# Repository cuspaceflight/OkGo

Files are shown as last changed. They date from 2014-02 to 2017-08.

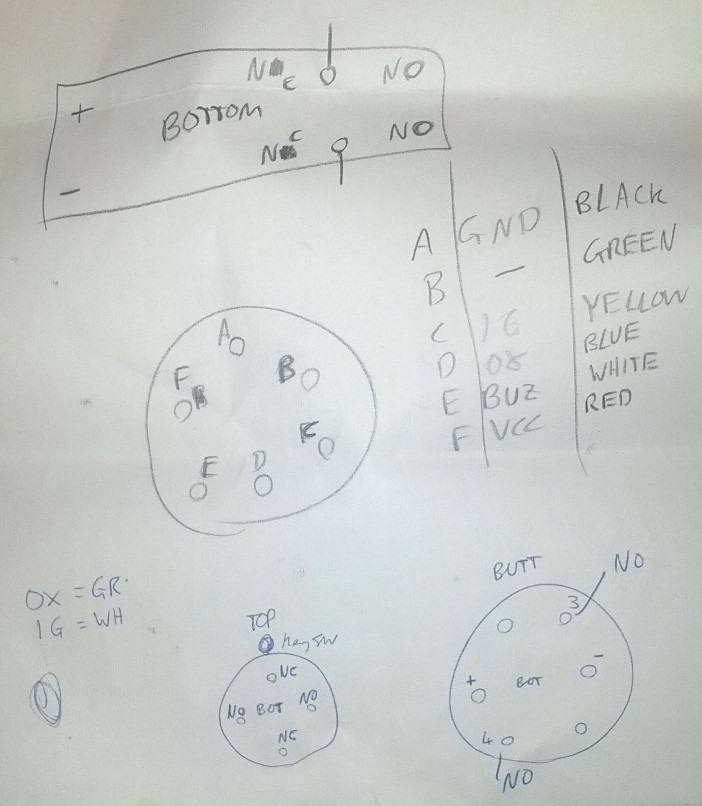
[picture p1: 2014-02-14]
OkGo/docs.jpg

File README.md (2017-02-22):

OkGo
====

*OkGo* is [Cambridge University Space Flight](http://cusf.co.uk)'s
rocket firing controller.

*OkGo* was designed for testing the *Quasar* hybrid rocket motor.  It allowed
remote (over 100m of wire) control of the nitrous oxide valve and firing of the
ignition e-match.  It was constructed using an ad-hoc point-to-point layout.
An entirely passive design, it simply uses mechanical switches to trigger
relays.  It was later upgraded to control two valves, one of which passed a low
flow of nitrous oxide to help start the motor.

*OkGo 2* was a full redesign for the launch of *Martlet 2*.  Due to the
increased safety radius (on the order of 500m) radio control is to be used.  It
will have 4 general purpose (valve or e-match) channels with independent
continuity checking and firing, and separate firing boxes containing current
limiting resistors.

*OkGo 3* is another full redesign for the launch of *Martlet 3*.  It will
continuity check and ignite a single channel with a constant-current drive.
Ignition and control will be small and light for portability.

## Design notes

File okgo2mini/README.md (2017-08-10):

# Design
* A mini version of OkGo 2 ignition, compatible with OkGo 2 control
* Use STM32F0 and RFM95W circuit from OkGo 2 ignition
    * If I'm careful I could make it pin-compatible and use the same firmware
      as OkGo 2, or just with minimal modification
* Use battery charge/management circuit from Toad/Linetime
    * Has only had minimal testing on Linetime. Wait for Toad to be tested
      before committing to this.
* Use 1A constant current firer from latest m3pyro
# Parts
* Nana plugs: red CN16308 black CN16305
* High retention red USB-B 1753809
* Red Hammond extruded aluminium case 2469292

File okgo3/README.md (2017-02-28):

# OkGo 3
## Features
* Single channel
* Continuity measurement
* Constant 4A current firing for e-matches
* Built-in battery (3.7V 2Ah)
* Charge from USB (400mA)
* Small and light
* Maybe easily detachable BNC antennas?
* Config and firmware upgrade over USB?

## Parts
* Case: Hammond 1553WCGY for control. Peli 1010 clear/yellow for ignition
* Battery: Cool Components 157 (Charge 400mA discharge 4A).
* Battery management bq24232HA
* Antenna: RF00075 ? Because it'll be easily detachable? But you really want it
  to be VPOL. And it's gross to put the BNC on the top.  Maybe same pivot
  swivel as on OkGo 2 Ignition?
* USB-B for charging because it's easy to clean the gunk out of.
* Ignition and control have touchscreen: ERC12864F7-4

## Thoughts
* Make both PCBs the same? They share the radio, battery, charging,
  on/off switch, case, USB, display and touchscreen
* Differences is ignition has banana jacks, control has fire button and
  keyswitch.
* Board-mount antenna connector on one end and cable-mount USB on other end
* Board mount nana jacks on front face or on one end?
* Control has display with touchscreen mounted to PCB which is mounted to top
  of the case, making display flush with top of case.  Antenna is an end-mount
  SMA which pokes out the end-panel.  Similarly for end-mount USB-B.
  Keyswitch, power switch and fire button???
* Ignition's touchscren is mounted to the board which sits in a sled in the
  bottom half of the peli - it's only accessible when you open the case.
  Charge USB is internal use only.  End-mount SMA goes to a pigtail to the
  external panel-mounted antenna SMA.
* Both have batteries mounted to the bottom of the PCB using a double-sided
  glue pad or possibly adhesive velcros.  Control's battery is in a void in the
  case, ignition's battery sits in a cut-out in the 3d printed sled.

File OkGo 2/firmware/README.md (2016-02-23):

OkGo2 Firmware
==============

# Getting started
## Grab the toolchain:
`sudo add-apt-repository ppa:terry.guo/gcc-arm-embedded`

`sudo apt-get update`

`sudo apt-get install gcc-arm-none-eabi`

**IF YOU FORGET TO ADD THE TERRY.GUO REPO YOU WILL GET MYSTERIOUS BUILD ERRORS
LIKE**

`arm-none-eabi-gcc: error: nano.specs: No such file or directory`

## Build libopencm3
* Run `git submodule update --init` to grab the libopencm3 repo
* Run `make` in `libopencm3/`
* **IF YOU FORGET THE PREVIOUS STEP YOU WILL GET MYSTERIOUS BUILD ERRORS LIKE**
  `No rule to make target 'main.elf'`.

## Setting a key
To authenticate both sides of the link, a symmetric pre-shared key is used.
This is stored in `common/key.h`.  An example file is provided at
`common/key_template.h`.  **The firmware will not build until a key
is set**.  To do this, copy `key_template.h` to `key.h`, change the key to
something random, and uncomment the relevant lines.

# Workflow
## Building firmware
* Run `make` in `control/` or `ignition/` as appropriate

## Programming
* `make flash` in `control/` or `ignition/` to program appropriate firmware
  using a BlackMagic programmer.

## Debugging
* More detailed info [_here_](http://darkdust.net/files/GDB%20Cheat%20Sheet.pdf)

### Getting started
* `make debug` to get an interactive debug session
* `arm-none-eabi-gdb foo.elf` or interactively `load foo.elf` and `file foo.elf`

### Printing info
* `p foo` / `print foo` to print `foo` in the current context
* `p/x foo` to print `foo` in hex

### Running
* `run` to run from beginning until break
* `start` to run until first line of `main()`
* `n` / `next` to step to next line
* `s` / `step` to step into a function
* `call myfunc()` to call a function

### Breaking
* `ctrl+c` to break wherever we happen to be
* `b function` / `b file.c:123` to add breakpoints on function call or line.
* `watch x` to break on change to variable `x`
* `d 1` to delete breakpoint 1
* `bt` / `where` for backtrace at current point

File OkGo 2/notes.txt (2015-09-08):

Firing cables
-------------
Banana jacks:
	Red: 1698956
	Yellow: 1698959
	Black: 1698957
Resistor:
	Need 2.5ohm with >60W handling
	RE03490 is 5ohm 50W for £1.5 - same as okgo1 I think.

Control 5V budget:
4x lightup button = 100mA
LCD = 150mA
total = 250mA

Control 3v3 budget:
30mA STM32
120mA RFM95W
337mA 5V budget scaled to 3v3
total = 487mA

Control battery wiring:
	Battery has JST-PH-F on short flying lead and sits on bottom half of case
	JST-PH-M Y-cable mounted on bottom half of case, to charge port on lower
	end-plate and to JST-PA on PCB.
	PCB routes battery via fuse to JST-PA for power button and then onwards.

STM32F071CBT Pin Assigning (control and ignition)
-------------
PC13,14,15 cannot source current and only sink 3mA and are limited to 2MHz into 30pF

USART locations:

10: USART4_TX
11: USART4_RX

12: USART2_TX
13: USART2_RX

21: USART3_TX
22: USART3_RX

ADC locations: pin 10-19 inc

SPI locations:

SPI1_NSS	14
SPI1_SCK 	15
SPI1_MISO	16
SPI1_MOSI	17

SPI1_NSS	38
SPI1_SCK	39
SPI1_MISO	40
SPI1_MOSI	41

SPI2_NSS	25
SPI2_SCK 	21
SPI2_MISO	27
SPI2_MOSI	28

SPI2_NSS	46
SPI2_SCK	26
SPI2_MISO	27
SPI2_MOSI	28

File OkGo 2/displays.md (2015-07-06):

#16x2:

    +----------------+
    |4.2V 6.4V  08/32|
    |ERR ERR ERR ERR |
    +----------------+
    +----------------+
    |4.2V 6.4V  08/32|
    |FIR OK  OK  ERR |
    +----------------+
    +----------------+
    |4.2V ?.?V  00/32|
    |    NO LINK     |
    +----------------+

#16x4:

    +----------------+
    |CBAT IBAT   RSSI|
    |4.2V 6.4V  08/32|
    |            CON |
    |FIR OK  OK  ERR |
    +----------------+
    +----------------+
    |CBAT IBAT   RSSI|
    |4.2V ?.?V  00/32|
    |    NO LINK     |
    |                |
    +----------------+

#20x2:

    +--------------------+
    |C4.2V I3.6V RSI08/32|
    |FIRE OK   OK   CERR |
    +--------------------+
    +--------------------+
    |C4.2V I?.?V RSI00/32|
    |      NO LINK       |
    +--------------------+

#20x4:

    +--------------------+
    |CBAT:4.2V  IBAT:6.4V|
    |    LINK: 08/32     |
    |CONT CONT CONT CONT |
    |ERR  ERR  ERR  ERR  |
    +--------------------+
    +--------------------+
    |CBAT:4.2V  IBAT:6.4V|
    |    LINK: 08/32     |
    |               CONT |
    |FIRE OK   OK   ERR  |
    +--------------------+
    +--------------------+
    |CBAT:4.2V  IBAT:?.?V|
    |    LINK: 00/32     |
    |      NO LINK       |
    |                    |
    +--------------------+

Possible metering display:

    +--------------------+
    |CBAT:4.2V  IBAT:6.4V|
    |    LINK: 08/32     |
    |FIRE OK   OK   ERR  |
    |9.4A 004R 125R 14kR |
    +--------------------+

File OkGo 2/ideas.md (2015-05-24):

#General Layout
 * Two boxes, *Control* (people end) and *Ignition* (rocket end)
 * 4 generic channels
 * AVR or Arduino pro-mini for control on each side.
 * Probably make each board with a custom PCB with everything onboard
 * Both boxes IP64/65 -- dust tight, protected against casual water ingress
 * Might be cute if the boxes can attach to a camera tripod -- apparent the
  thead on this is "1/4-20 UNC" for standard consumer tripods.

#Radio Link
 * Up to 500m apart on vaguely flat terrain with no particularly gnarly
  blockages inbetween
 * SMA-mount swivel rubber ducky antennas on each end.
 * LORA sounds like a good thing for the radio link -- spread spectrum
   goodness.
 * 868MHz would be nicer than 433MHz so we can stay away from FRS/ham radios
 * Might as well go with 20dBm = 100mW if we can.
 * [HopeRF RFM95W-868](http://www.hoperf.co.uk/shop/RFM95W-868S2-RFM95W_868S2.html)
   is 20dBm 868MHz LORA, sounds thoroughly excellent.  Not cheap though.

#Power Supply
 * Both boxes with integrated LiPOs
    * Probably 3-4S in ignition to approximate the 12V most things want
    * 1S in control (makes it easier because control doesn't need balance
      charging, and 1S will happily LDO down to 3v3).
 * Charged by external standard balance charger
 * Exposing balance charge connections via custom 4-contact connection
  (only need about an amp per contact).
 * Make special cable from custom connector to 3S balance + two banana
  jacks

#Control Box
 * Nice key-switch to power the box and arm.
 * Indication of link status / arm -- bi-colour red/green LED
 * Indication of continuity per-channel -- bi-colour red/green LED in/on or
  next to each firing button.

#Ignition Box
 * Current arming system with beeper and extra loud/quiet switch
 * No integrated current limiting for e-matches, all 4 channels are
  generic 12V some amps brought out to banana screwdowns.
 * For connecting to e-matches use a banana to croc clip lead with
  integrated current limit resistor.  Firey end has banana plugs with
  replacable croc clips for when they get gnarly.

#Micros
 * STM32F071CBT6 seems legit, costs about £2.50, LQFP-48.
 * [The Insider's Guide to the STM32](http://www.hitex.com/fileadmin/pdf/insiders-guides/stm32/isg-stm32-v18d-scr.pdf)
   seems like a helpful getting started document.
 * [Onecall](http://onecall.farnell.com/stmicroelectronics/stm32f071cbt6/mcu-32bit-cortex-m0-48mhz-lqfp/dp/2432093)
   and [datasheet](http://www.farnell.com/datasheets/1835716.pdf).
 * I should read [this](http://www.st.com/web/en/resource/technical/document/application_note/CD00221665.pdf) about STM32 oscillators
 * RFM95W seems to have listed pin directions backwards for MISO/MOSI in
   datasheet.

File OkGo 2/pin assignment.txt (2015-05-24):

pin name in backets means reset has different function
FT = 5V tolerant IO
FTf = 5V tol IO FM+ capable
TTa = 3v3 tolerant ADC
TC = 3v3

PC14/PC15 default to OSC32

PA0-3: TTa
PA8-12: FT

PB0-1: TTA
PB2: FT
PB10-12: FT
PB13-14: Ftf
PB15: FT

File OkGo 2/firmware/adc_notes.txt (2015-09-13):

adc notes

12-bit adc
internal channels: V_ref, temperature, VBAT (VDD)
Single shot or scan, latter performs automatic conversion on a group of analog inputs.
Can be DMAed
Result stored in left- or right-aligned 16-bit register (set ALIGN in ADC_CFGR1 to decide)
Choose resolution 12- 10- 8- 6-bit
1us conversion for 12-bit and faster for lower res.
Use RES[1:0] in ADC_CFGR1 to set resolution

When ADC is disabled (ADEN=0), calibrate by setting ADCAL=1, then leave the ADC alone until calibration finishes and ADCAL=0.

Only touch ADEN and ADCAL when ADC is disabled
Only touch ADSTART and ADDIS when ADC enabled and no pending disable request
Only touch other config bits (ADC_*) when ADEN=1 and ADSTART=0 (no ongoing conversion)
Only touch ADSTP if ADC enabled and no pending disable request.

Select scan channels using CHSEL (set bits for channels we want, CH0-18) and SCANDIR

Program sampling time to allow sampling capacitor to charge, based on impedance of source.  ADC_SMPR->SMP[2:0] sets sample time as a number of ADC clock cycles.  Sample time is common to all channels.
Analog switch has R=1k and sampling capacitor is 8pF.  Input impedances are on the order of 10k.  This gives a 99% rise-time of 400ns.  

Dedicated ADC clock is 14MHz making each ADC clock 71ns.  For our 99% rise we need 400/71=6 ADC clocks, so go with 13.5.

For continuous conversion, set CONT=1 in ADC_CFGR1 then ADSTART=1 and it will go and go and go.  Each conversion result is stored in ADC_DR and an interrupt optionally interrupts.
EXTEN = 0x0 for software-only triggering.

Normal strobe ADCing just dumps everything into the same ADC_DR register.  For easy readback you need to DMA it to a circular buffer.

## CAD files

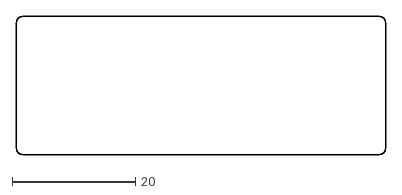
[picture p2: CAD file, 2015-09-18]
OkGo 2/cam/control_window_laser.dxf
60.0 x 22.5

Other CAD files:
OkGo 2/control/gerbers/control-F_Paste.dxf
OkGo 2/ignition/gerbers/ignition-F_Paste.dxf

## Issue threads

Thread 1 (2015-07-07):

De-specify SPI pins

cillian64, 2015-07-07:
On STM32F072 part, make the SPI pins not specified on the schematic part, as there are several choices for each.  I should also choose more carefully which pins I use based on PCB layout.

Closed 2015-07-07.

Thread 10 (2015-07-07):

Connect up nRST from SWDIO connector to STM32?

cillian64, 2015-07-07:

cillian64, 2015-07-08:
Yep, definitely.  This is (almost) correct (typo) on control, and apparently missing on ignition

Closed 2015-07-08.

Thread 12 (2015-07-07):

Relay failsafe circuit

cillian64, 2015-07-07:
Upstream relay on battery supply to firing relays.  Connect a sense line (with pulldown weaker than the 10k 3v3 sense pull-up) to the distribution between upstream and firing relays.  If any relays are welded this sense line will appear high while all relays are un-energised.

Closed 2015-07-08.

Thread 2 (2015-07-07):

Sort out mechanics

cillian64, 2015-07-07:
Think about cases for both sides, how to mount boards and switches and all the rest (panel mount, PCB mount?), how cases open and close, wire/board/panel connectors.

cillian64, 2015-08-14:
Control: start with display hole down. display bolts to standoffs on back of PCB, which bolts to standoffs on case's mounting lugs.  Arm, LED, keyswitch, firing buttons, all screw through front of case. Antenna goes through top plate, charge connector on bottom plate. Battery velcros to inside of case, probably on back half.

cillian64, 2015-08-14:
Ignition: Bottom of box is concave side.  PCB screws down to bottom brass-insert lugs covering entire bottom.  LiPO velcros and/or cable ties to PCB.  Antenna sticks out a side, everything else mounts through lid.

Closed 2015-08-14.

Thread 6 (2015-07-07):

Specify mechanical parts inc fixings

cillian64, 2015-07-07:

cillian64, 2015-08-20:
Ignition fixings:
4x 2x M? for neutriks
4x M3 for board to case

Control fixings:
2-4x M3 standoffs for board-case
2-4x M3 for board-standoffs
2-4x M? standoffs for LCD-board
2-4x M? screws for LCD-board

cillian64, 2015-08-27:
Screws Summary:
* 8x M3x20 pozi CS
* 4x M3x12 pozi pan/cheese
* 4x M3x6 pan
* 4x M3.5x12 pan

Nuts summary:
* 12x M3 full nuts
* lots x M3.5 full nuts

Washers summary:
* 24x M3 plain washers
* lots x M3.5 plain washers

cillian64, 2015-08-27:
Ordered

Closed 2015-08-27.

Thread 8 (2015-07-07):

Choose some connectors and stuff

cillian64, 2015-07-07:

cillian64, 2015-08-06:
Remaining:
Control
 - [ ] control charge
Ignition
 - [ ] ignition charge
 - [ ] ignition power-to-board
 - [ ] ignition firing
 - [ ] ignition firing-to-board

Closed 2015-08-14.

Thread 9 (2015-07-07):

Confirm footprints

cillian64, 2015-07-07:

cillian64, 2015-08-17:
Ignition:
 - SOD-123F [ ]
 - SOD-134FL [ ]
 - Switching reg [ ]
 - Relays [ ]
 - Fuse [ ]
 - JST-PA-2 upright [ ]

cillian64, 2015-08-17:
Control:
 - MSOP8 [ ]
 - JST-PA-2 RA [ ]
 - JST-PA-4 RA [ ]
 - Trimpot [ ]
 - LCD [ ]
 - Hammond 1553T [ ]
 - Polyfuse [ ]
 - Switching booster [ ]

cillian64, 2015-08-17:
Common:
 - R0805 [ ]
 - C0805 [ ]
 - C1206 [ ]
 - TVS 0603 [ ]
 - LQFP48 footprint [ ] pinout [ ]
 - RFM95W footprint [ ] pinout [ ]
 - SOT23 [ ]
 - Crystal [ ]
 - SMA-F [ ]
 - SWD [ ]
 - TP [ ]

Closed 2015-08-18.

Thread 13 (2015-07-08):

Add ESD diodes

adamgreig, 2015-07-08:
Should protect all the connectors with ESD diodes, especially power, antennas and firing channels. I like Farnell 2368169.

cillian64, 2015-07-08:
Similarly, remove the current pulldowns on the ignition outputs, they are entirely pointless.

cillian64, 2015-07-08:
I've been sneezing a lot lately so I'll get the 0603, [2368174](http://onecall.farnell.com/bourns/cga0603mlc-24e/esd-suppressor-0603-24v-0-5pf/dp/2368174).

Closed 2015-07-08.

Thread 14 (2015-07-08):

Test points

cillian64, 2015-07-08:

cillian64, 2015-07-08:
RFM and LCD are already easy enough to probe

Ignition: Vbatt, GND, 3v3, nRST, CONT_CH*, UPSTREAM_RELAY, RELAY_SENSE, FIRING_DIST, Firing channel outputs.

Control: Vbatt, GND, 3v3, nRST

Closed 2015-07-08.

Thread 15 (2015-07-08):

Check if drive resistor is on correct side of crystal / OSC_IN/OSC_OUT

cillian64, 2015-07-08:

Closed 2015-07-08.

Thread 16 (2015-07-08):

higher precision resistors for battery monitor

cillian64, 2015-07-08:
Accidentally used 5% resistors for the battery monitor divider, which is pretty poor...

cillian64, 2015-07-08:
Resolved.

Closed 2015-07-08.

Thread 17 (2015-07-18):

Change footprints to non-handsoldering

cillian64, 2015-07-18:
Will almost certainly mess up / have too much paste.

Closed 2015-07-18.

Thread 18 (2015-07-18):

Relay flyback diodes?

cillian64, 2015-07-18:

cillian64, 2015-07-18:
With flyback diode: ~1H coil (estimated from similar AC coil specs) gives 5mJ coil energy, dissipating in 0.015s in the coil resistance.

Closed 2015-07-18.

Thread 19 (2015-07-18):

USB interface

cillian64, 2015-07-18:
Bring GND,RX,TX,3v3 from STM32 UART to a JST-PA header on the board.

Connect this to some sort of 3-way or 4-way connector on the case.

Closed 2015-07-29.

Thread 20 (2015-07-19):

fix booster

cillian64, 2015-07-19:
5V "booster" is not actually a 5v booster.  Also check it's up to 250mA / 1.5W

boyuanxiao, 2015-07-21:
Is this about the Murata chip?  It looks alright: http://uk.mouser.com/ProductDetail/Murata-Power-Solutions/MEJ2S0305SC/?qs=pitIP5Ybo%2F%252bvVODbaEhTwg%3D%3D (sorry if you've already checked this...)

But if the ground is the same on either side it could be cheaper to go for a non-isolated converter?

cillian64, 2015-07-21:
Yep, this issue was before I updated the part  -- previously I'd accidentally put on a 3v3 - 3v3 converter (which was also not up to the current of all the LEDs and the LCD backlight!).  I forgot to close the issue when I fixed that.

A non-isolated converter would work fine but I didn't find one as convenient on my brief search of farnell.  I am open to suggestions.

cillian64, 2015-07-21:
(fixed in d90080b024b719421ce510433d57c2e19026046a)

boyuanxiao, 2015-07-21:
Cool - looks like most step up regulators which are cheaper will require getting the right inductors etc. Probably not worth the hassle if you're only getting one.

cillian64, 2015-07-21:
Yep, cost is quite low down on my priorities, so it's all about the convenience of something that Just Works (and it helps that it's a pretty small footprint compared to a DIY switch-mode booster)

Closed 2015-07-21.

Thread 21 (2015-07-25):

LCD voltages

cillian64, 2015-07-25:
Control's LCD is 5V.  Should be no problem to power VDD and V_LCD and V_LED from the 5V converter and it's V_IL is <3V so inputs are fine.  If we ever read back from it the respective STM32 pins will need to be 5V tolerant or otherwise clamped.  Do we ever need/want to read back from the display?

cillian64, 2015-07-29:
Clamped to read-only -- no problem.

Closed 2015-07-29.

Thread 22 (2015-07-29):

Make mechanical holes have correct clearance markers and unmask

cillian64, 2015-07-29:

cillian64, 2015-08-14:
Done as far as possible on control, not yet on ignition.

Closed 2015-08-15.

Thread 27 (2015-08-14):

Think about antenna connections and waterproofing

cillian64, 2015-08-14:

cillian64, 2015-08-17:
Waterproofing should be okay with an SMA gasket and hope the antenna copes -- easy enough to swap out if not and might be able to caulk up the joint.

Will worry more about SMA-F length when I have the ignition case and SMA-F and ANT.

cillian64, 2015-08-18:
Ignition will use vertical SMA with a pigtail (to be found).  Control happily fits with the end-plate.  Simple SMA gasket on both and hope for the best with the antenna.

Closed 2015-08-18.

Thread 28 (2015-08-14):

Routing of decoupling capacitors

cillian64, 2015-08-14:
Route power/ground to decoupling caps, not directly to pins.

Route to largest cap then down to smallest then to IC pins.  Where possible.

Closed 2015-08-14.

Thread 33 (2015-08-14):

Prep and order parts

cillian64, 2015-08-14:
Big farnell BOM
Arrange SWDs (from adam?)
RFM95Ws from hoperf.co.uk
Ignition case from Rapid/RS

cillian64, 2015-08-20:
Basically done.

Closed 2015-08-20.

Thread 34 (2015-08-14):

Design packet format

cillian64, 2015-08-14:
Fixed size/format packets, one from ignition->control, one control->ignition.

Basic inspiration: control sends packet ID, arm/disarm, fire ch1/ch2/ch3/ch4 every X interval
Ignition replies with same ID (as ack), cont ch1/ch2/ch3/ch4, batt voltage, relay sense, RSSI

cillian64, 2015-08-21:
First draft of protocols in 9c2f3c5

cillian64, 2015-09-15:
Seems like this has settled down.

Closed 2015-09-15.

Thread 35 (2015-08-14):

Lay out structure/flow of both firmwares

cillian64, 2015-08-14:

cillian64, 2015-08-21:
9c2f3c5 describes what's going on, now write skeletons

cillian64, 2015-09-18:
Give ignition a non-blocking receive and handle packet drops using a timer-check.  Nonblocking also means we can handle beepering

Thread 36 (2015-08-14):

Double-check DRC and ERC with correct design parameters

cillian64, 2015-08-14:

cillian64, 2015-08-18:
Relevant things:
 - Track width: .2mm / 8mil
 - Track gap/clearance: .2mm / 8mil
 - Min annular ring: .3mm / 12mil (CHECK VIAS)
 - Min hole: .4mm / 16mil (after plating)
 - Resist clearance: .08mm / 3mil
 - Min silk width: .15mm / 6mil

Closed 2015-08-19.

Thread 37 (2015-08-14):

I made a note that RFM95Ws have incorrect pin directions in datasheets -- double check this

cillian64, 2015-08-14:

cillian64, 2015-08-17:
Moved to confirm footprints, Issue #9

Closed 2015-08-17.

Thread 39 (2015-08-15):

put trimpot on ignition for buzzer

cillian64, 2015-08-15:
put mosfet series resistor before trimpot so turning volume down doesnt just ground stm32 output pin

cillian64, 2015-08-17:
Going to do this in software with the new control config menu.

Closed 2015-08-17.

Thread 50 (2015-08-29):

Correct LCD delays to appropriate us values

cillian64, 2015-08-29:
Actually enable crystal oscillator. Re"calibrate" delay functions and make a delay_us function and make LCD stuff use appropriate microsecond delays.

Closed 2015-09-13.

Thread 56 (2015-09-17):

Timers/timing based on sysclock instead of delays

cillian64, 2015-09-17:
For stuff like packet rate and the buzzer we want to have async delays based on sysclock, not delay_?s()

Closed 2015-09-19.

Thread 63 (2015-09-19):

Complain of booted armed

cillian64, 2015-09-19:
Control should refuse to turn on when armed,unless rebooting due to watchdog timer.

cillian64, 2015-09-19:
Resolved in 98670fe

Closed 2015-09-19.

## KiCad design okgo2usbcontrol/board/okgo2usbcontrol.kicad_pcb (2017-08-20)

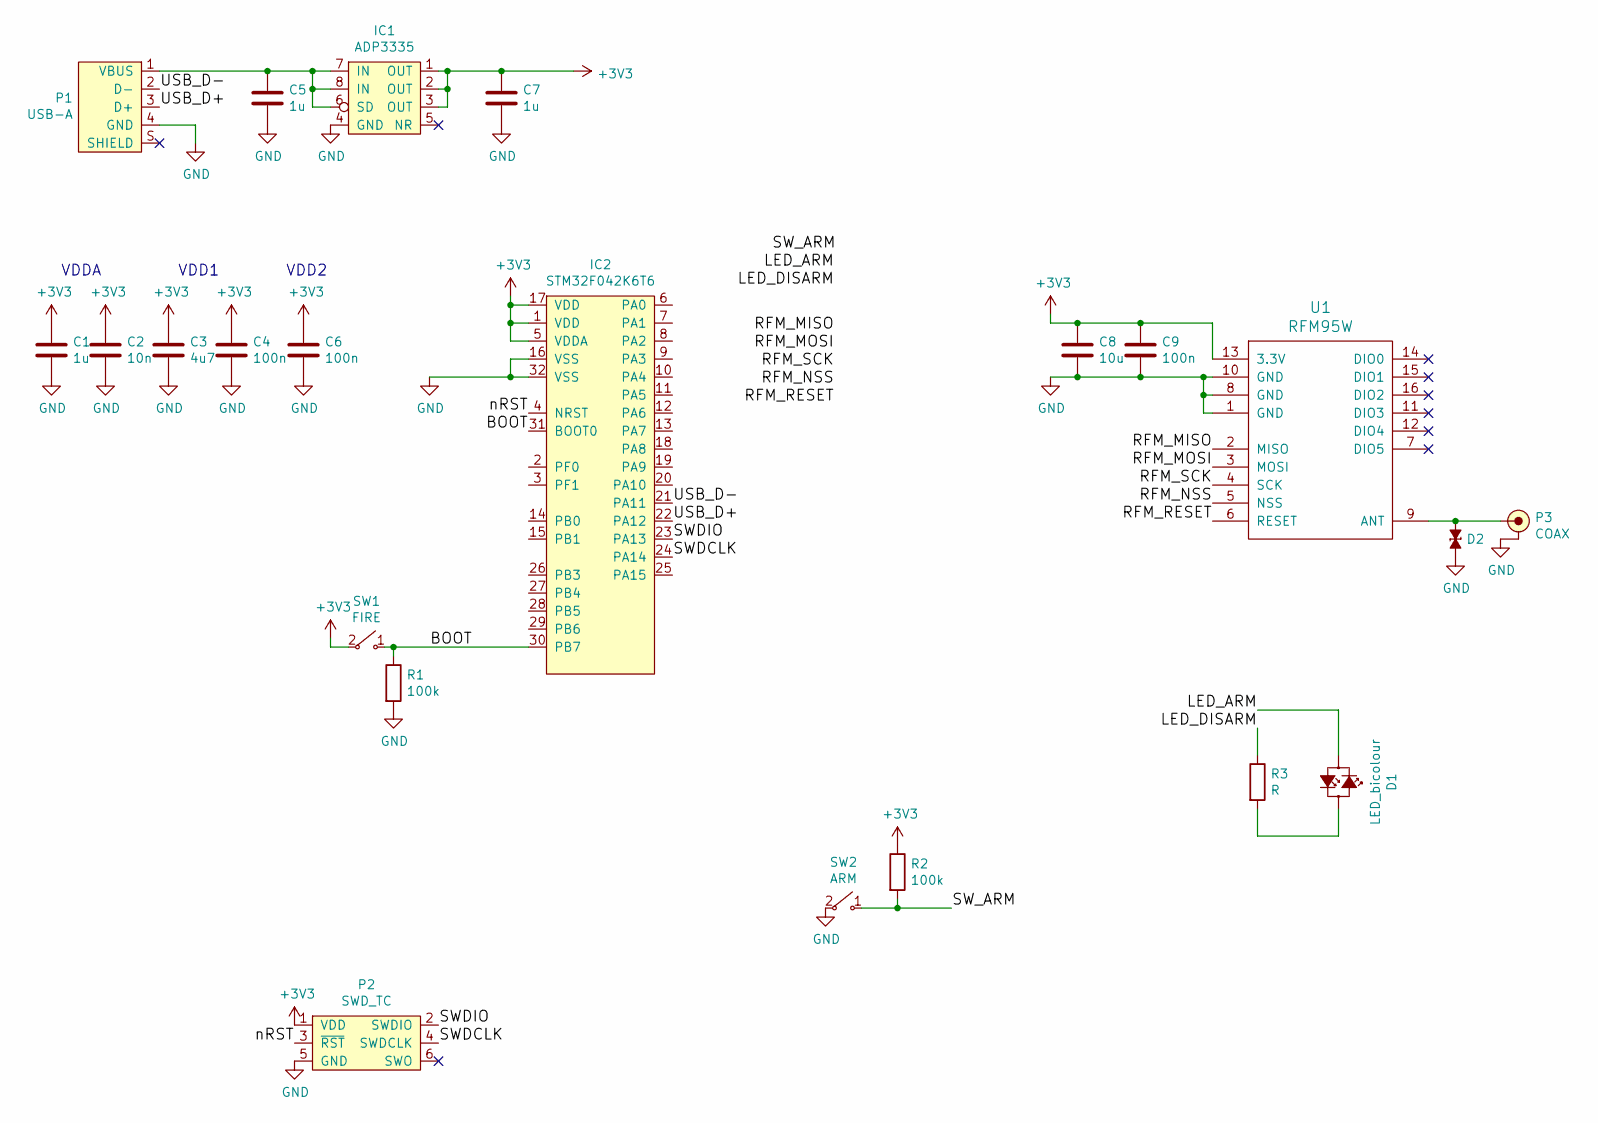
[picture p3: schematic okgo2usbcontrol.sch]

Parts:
C1, C5, C7: 1u; 0603
C2: 10n; 0603
C3: 4u7; 0603
C4, C6, C9: 100n; 0603
C8: 10u; 0603
D1: LED_bicolour; 0805-LED
D2: ESD_DIODE; 0603
IC1: ADP3335; MSOP-8; Farnell 2067775
IC2: STM32F042K6T6; LQFP-32; Farnell 2750629
P1: USB-A; USB-A_M_Edge; Farnell 2067044
P2: SWD_TC; TC2030-NL
P3: COAX; SMA-EDGE; Farnell 1608592
R1, R2: 100k; 0603
R3: R; 0603
SW1: FIRE; FSM2JSMx; Farnell 2610947
SW2: ARM; JSX08001SAQNL; Farnell 2435152
U1: RFM95W

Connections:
+3V3: C1.1, C2.1, C3.1, C4.1, C6.1, C7.1, C8.1, C9.1, IC1.1 (OUT), IC1.2 (OUT), IC1.3 (OUT), IC2.1 (VDD), IC2.5 (VDDA), IC2.17 (VDD), P2.1 (VDD), R2.1, SW1.2, U1.13 (3.3V)
/BOOT: IC2.30 (PB7), IC2.31 (BOOT0), R1.1, SW1.1
/LED_ARM: D1.1 (K)
/LED_DISARM: R3.1
/RFM_MISO: U1.2 (MISO)
/RFM_MOSI: U1.3 (MOSI)
/RFM_NSS: U1.5 (NSS)
/RFM_RESET: U1.6 (RESET)
/RFM_SCK: U1.4 (SCK)
/SWDCLK: IC2.24 (PA14), P2.4 (SWDCLK)
/SWDIO: IC2.23 (PA13), P2.2 (SWDIO)
/SW_ARM: R2.2, SW2.1
/USB_D+: IC2.22 (PA12), P1.3 (D+)
/USB_D-: IC2.21 (PA11), P1.2 (D-)
/nRST: IC2.4 (NRST), P2.3 (~RST)
GND: C1.2, C2.2, C3.2, C4.2, C5.2, C6.2, C7.2, C8.2, C9.2, D2.2, IC1.4 (GND), IC2.16 (VSS), IC2.32 (VSS), P1.4 (GND), P2.5 (GND), P3.2 (GND), R1.2, SW2.2, U1.1 (GND), U1.8 (GND), U1.10 (GND)
unnamed: C5.1, IC1.6 (SD), IC1.7 (IN), IC1.8 (IN), P1.1 (VBUS)
unnamed: D1.2 (A), R3.2
unnamed: D2.1, P3.1 (RF), U1.9 (ANT)

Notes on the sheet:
VDDA
VDD1
VDD2

Board: 2 copper layers, 22 parts (3 on the bottom side), 12 nets, no tracks yet.

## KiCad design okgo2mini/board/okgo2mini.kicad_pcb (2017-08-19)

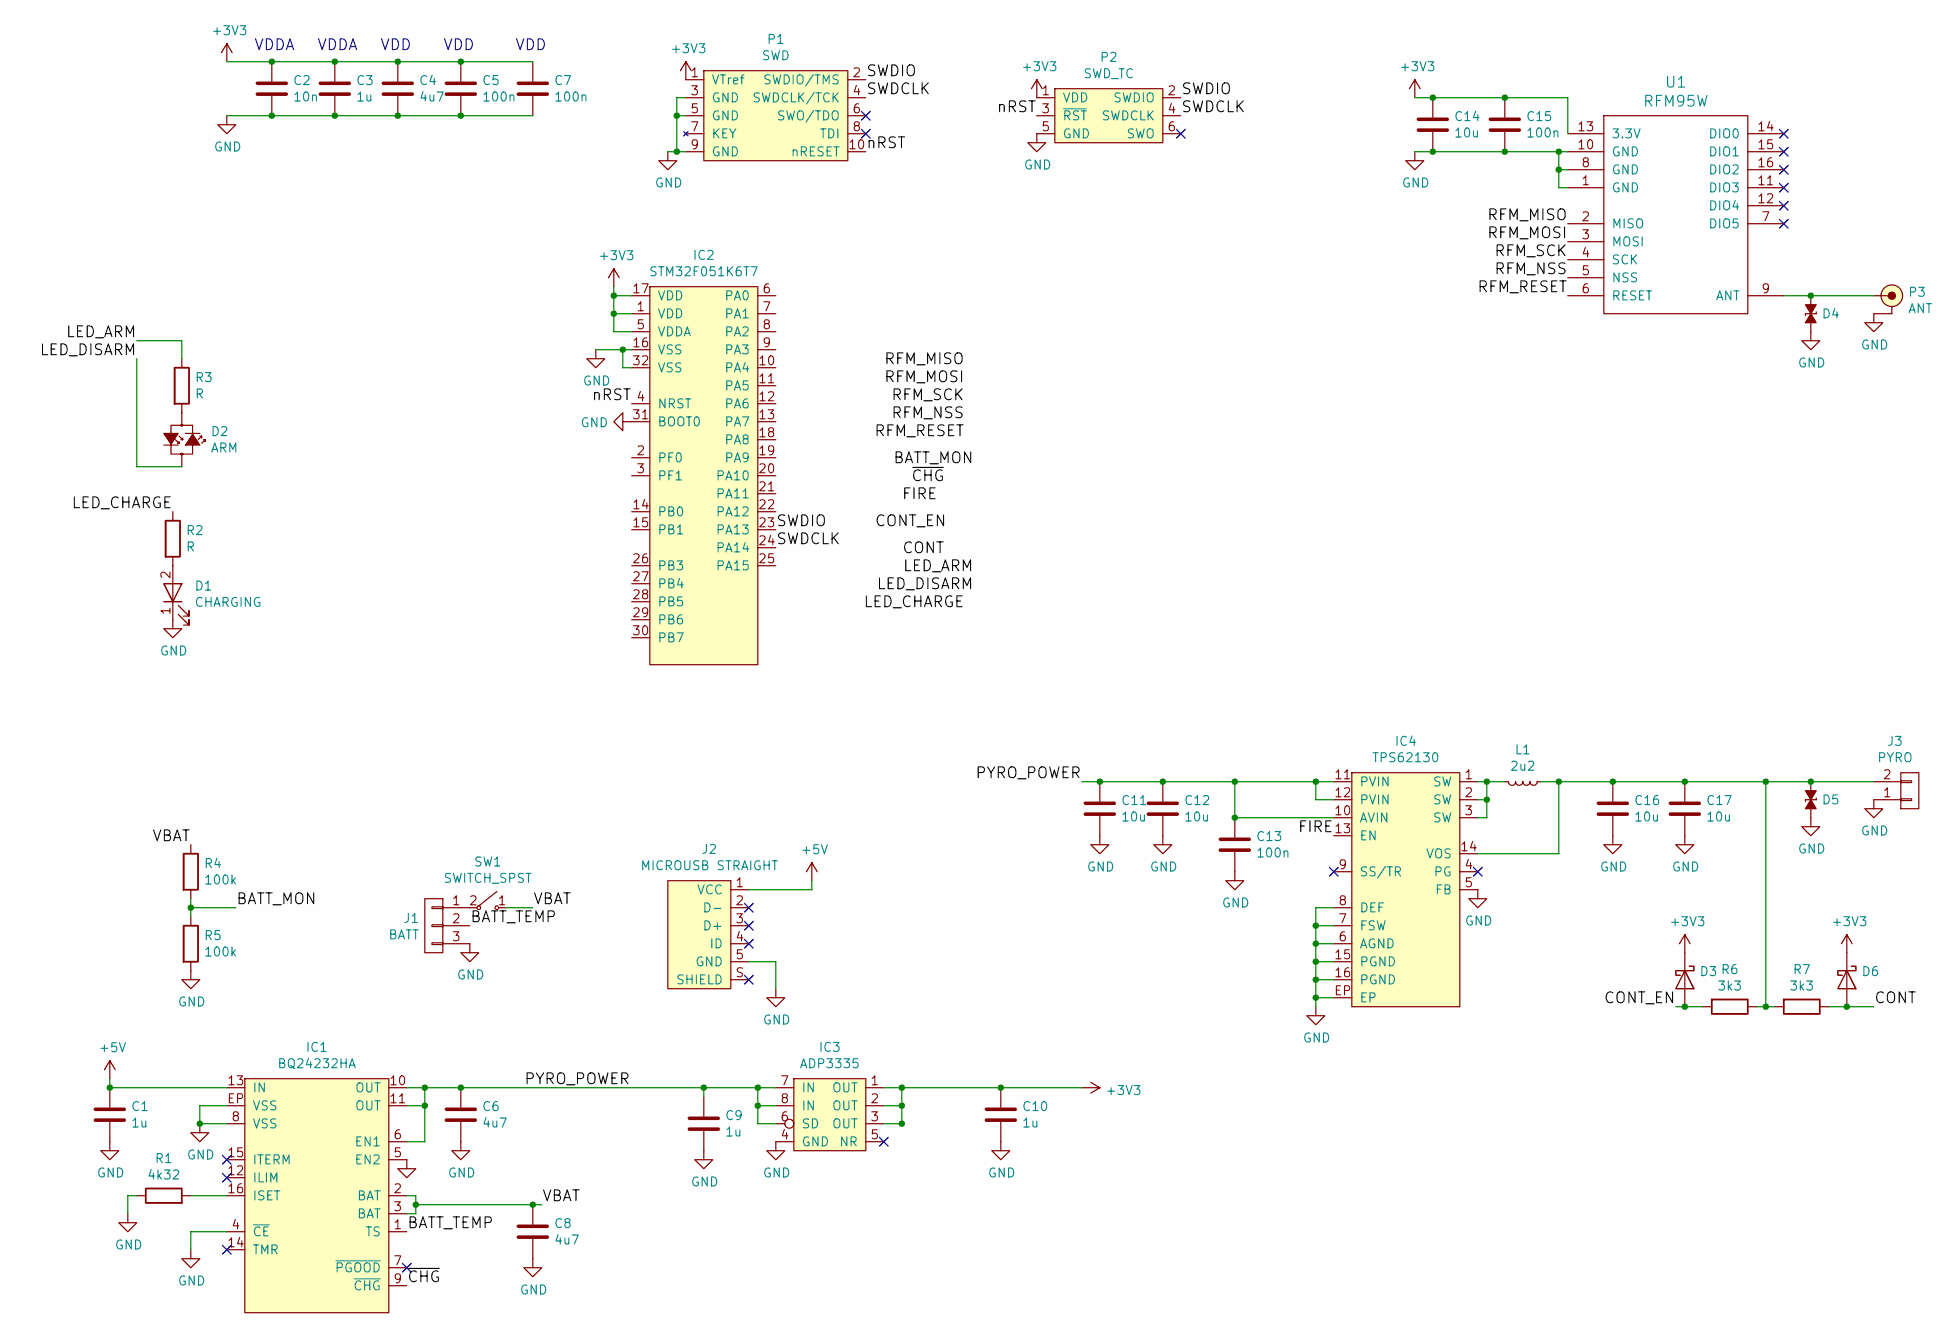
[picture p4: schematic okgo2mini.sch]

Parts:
C1, C3, C9, C10: 1u; 0603
C2: 10n; 0603
C4, C6, C8: 4u7; 0603
C5, C7, C13, C15: 100n; 0603
C11, C12, C14, C16, C17: 10u; 0603
D1: CHARGING; 0805-LED; Farnell 2610420
D2: ARM; 0805-LED; Farnell 2079908
D3, D6: PMEG2005AEA; SOD-323; Farnell 8737843
D4, D5: ESD_DIODE; 0603
IC1: BQ24232HA; QFN-16-EP-TI; Farnell 2576286
IC2: STM32F051K6T7; LQFP-32; Farnell 2432085
IC3: ADP3335; MSOP-8; Farnell 2067775
IC4: TPS62130; QFN-16-EP-TI; Farnell 2361246
J1: BATT; S03B-PASK-2
J2: MICROUSB STRAIGHT; USB_Micro_B_Vertical; Farnell 2614949
J3: PYRO; S02B-PASK-2
L1: 2u2; XFL4020; Farnell 2289216
P1: SWD; FTSH-105-01-F-D-K
P2: SWD_TC; TC2030-NL
P3: ANT; SMA-EDGE; Farnell 1608592
R1: 4k32; 0603
R2, R3: R; 0603
R4, R5: 100k; 0603
R6, R7: 3k3; 0603
SW1: SWITCH_SPST; 710xxxxV3xx; Farnell 9574743
U1: RFM95W

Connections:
+3V3: C2.1, C3.1, C4.1, C5.1, C7.1, C10.1, C14.1, C15.1, D3.1 (K), D6.1 (K), IC2.1 (VDD), IC2.5 (VDDA), IC2.17 (VDD), IC3.1 (OUT), IC3.2 (OUT), IC3.3 (OUT), P1.1 (VTref), P2.1 (VDD), U1.13 (3.3V)
+5V: C1.1, IC1.13 (IN), J2.1 (VCC)
/BATT_MON: R4.2, R5.1
/BATT_TEMP: IC1.1 (TS), J1.2
/CONT: D6.2 (A), R7.1
/CONT_EN: D3.2 (A), R6.2
/FIRE: IC4.13 (EN)
/LED_ARM: R3.1
/LED_CHARGE: R2.1
/LED_DISARM: D2.2 (A)
/PYRO_POWER: C6.1, C9.1, C11.1, C12.1, C13.1, IC1.6 (EN1), IC1.10 (OUT), IC1.11 (OUT), IC3.6 (SD), IC3.7 (IN), IC3.8 (IN), IC4.10 (AVIN), IC4.11 (PVIN), IC4.12 (PVIN)
/RFM_MISO: U1.2 (MISO)
/RFM_MOSI: U1.3 (MOSI)
/RFM_NSS: U1.5 (NSS)
/RFM_RESET: U1.6 (RESET)
/RFM_SCK: U1.4 (SCK)
/SWDCLK: IC2.24 (PA14), P1.4 (SWDCLK/TCK), P2.4 (SWDCLK)
/SWDIO: IC2.23 (PA13), P1.2 (SWDIO/TMS), P2.2 (SWDIO)
/VBAT: C8.1, IC1.2 (BAT), IC1.3 (BAT), R4.1, SW1.1
/nRST: IC2.4 (NRST), P1.10 (nRESET), P2.3 (~RST)
/~CHG: IC1.9 (~CHG)
GND: C1.2, C2.2, C3.2, C4.2, C5.2, C6.2, C7.2, C8.2, C9.2, C10.2, C11.2, C12.2, C13.2, C14.2, C15.2, C16.2, C17.2, D1.1 (K), D4.2, D5.2, IC1.4 (~CE), IC1.5 (EN2), IC1.8 (VSS), IC1.EP (VSS), IC2.16 (VSS), IC2.31 (BOOT0), IC2.32 (VSS), IC3.4 (GND), IC4.5 (FB), IC4.6 (AGND), IC4.7 (FSW), IC4.8 (DEF), IC4.15 (PGND), IC4.16 (PGND), IC4.EP, J1.3, J2.5 (GND), J3.1, P1.3 (GND), P1.5 (GND), P1.9 (GND), P2.5 (GND), P3.2 (GND), R1.1, R5.2, U1.1 (GND), U1.8 (GND), U1.10 (GND)
unnamed: C16.1, C17.1, D5.1, IC4.14 (VOS), J3.2, L1.1, R6.1, R7.2
unnamed: D1.2 (A), R2.2
unnamed: D2.1 (K), R3.2
unnamed: D4.1, P3.1 (RF), U1.9 (ANT)
unnamed: IC1.16 (ISET), R1.2
unnamed: IC4.1 (SW), IC4.2 (SW), IC4.3 (SW), L1.2
unnamed: J1.1, SW1.2

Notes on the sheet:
VDDA
VDD

Board: 2 copper layers, 43 parts (0 on the bottom side), 19 nets, no tracks yet.

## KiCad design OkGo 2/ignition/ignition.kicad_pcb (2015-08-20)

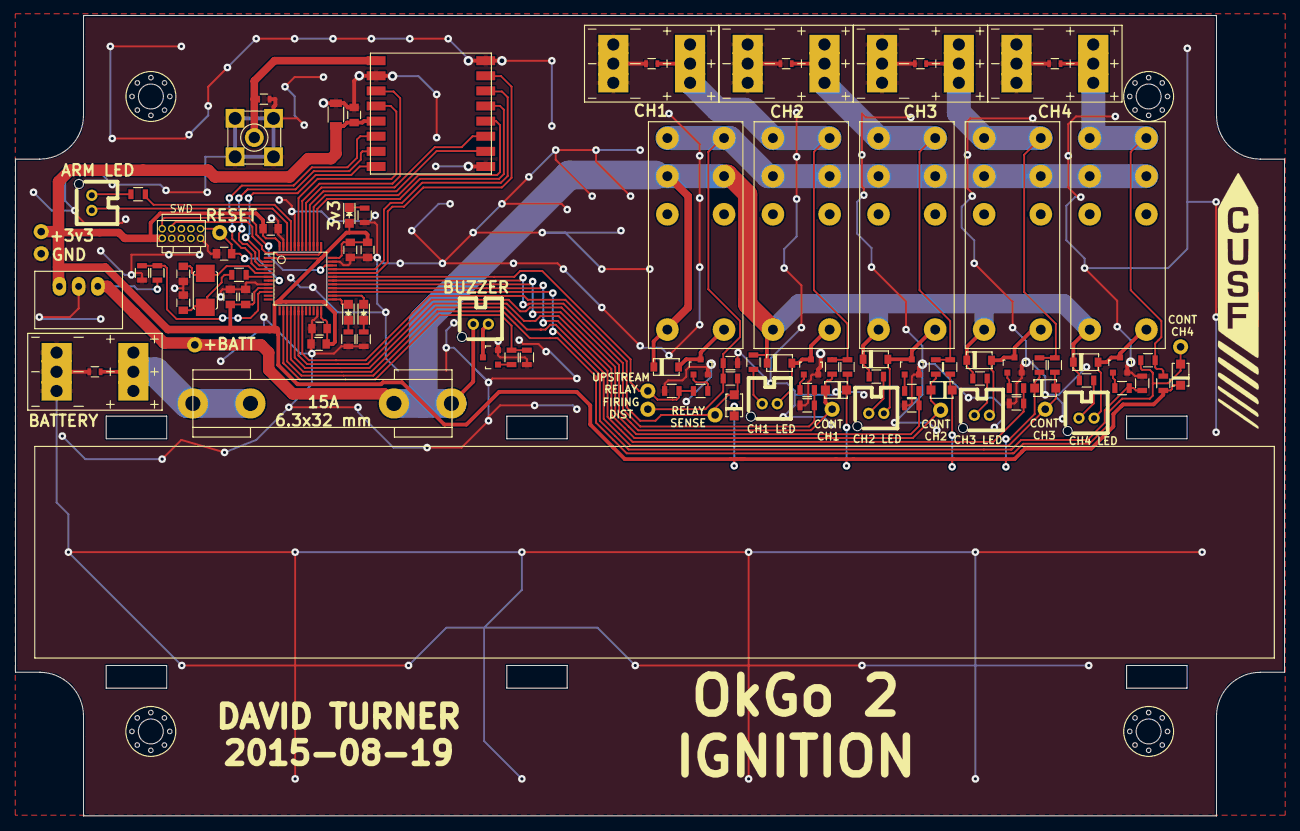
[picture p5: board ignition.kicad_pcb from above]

Board: 2 copper layers, 167.9 x 105.9 mm, 108 parts (0 on the bottom side), 63 nets.

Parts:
C101, C102, C104, C105, C109: 100n; C_0805
C103, C106: 4u7; C_0805
C107: 10n; C_0805
C108: 100u; C_1206
C110: 1u; C_0805
C111, C112: 15p; C_0805
D101, D103, D206, D210, D214, D218: TVS_small; R_0603
D104: RED; LED-0805
D105: GREEN; LED-0805
D106: YELLOW; LED-0805
D201, D205, D209, D213, D217: MBR2H200SFT1G; SOD-123FL
D202, D204, D208, D212, D216: D; SOD-123F
F101: 6.3x32; 6x32_fuseclip
K201, K202, K203, K204, K205: 16A SPST; Relay_RT314
M3_MOUNT, M3_MOUNT#2, M3_MOUNT#3, M3_MOUNT#4: VAL**; M3_MOUNT_FANCY
P105: BATT; PCB_SPADE
P107: ARM_LED; JST-PA-2-VERT
P109: BUZZ; JST-PA-2-VERT
P111: SMA; SMA_upright
P201: CH3_LED; JST-PA-2-VERT
P203: CH3; PCB_SPADE
P204: CH1_LED; JST-PA-2-VERT
P206: CH1; PCB_SPADE
P207: CH4_LED; JST-PA-2-VERT
P209: CH4; PCB_SPADE
P210: CH2_LED; JST-PA-2-VERT
P212: CH2; PCB_SPADE
Q101, Q201, Q202, Q203, Q204, Q205: BSS138BK; SOT-23
R101, R207, R212, R217, R222: 10k; R_0805
R102: 3k3; R_0805
R103: 75R; R_0805
R104: 100R; R_0805
R105, R201, R208, R213, R218, R223: 180R; R_0805
R106, R202, R204, R210, R214, R220, R224: 100k; R_0805
R107, R108, R109: R; R_0805
R203, R206, R211, R216, R221: 1k; R_0805
R205, R215: 430; R_0805
R209: 510R; R_0805
R219: 510; R_0805
TP101: BATT; TESTPOINT
TP102: GND; TESTPOINT
TP103: nRST; TESTPOINT
TP104: 3v3; TESTPOINT
TP201: FiringDist; TESTPOINT
TP202: USRelay; TESTPOINT
TP203: RelaySense; TESTPOINT
TP204: ContCH3; TESTPOINT
TP205: ContCH1; TESTPOINT
TP206: ContCH4; TESTPOINT
TP207: ContCH2; TESTPOINT
U103: SWD; FTSH-105-01-F-D-K
U105: RFM95W
U106: STM32F071CBT6; LQFP48_ST
U107: TSR 0.5-2433; TSR-0_5
Y101: 8MHz; XTAL50x32

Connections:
+3V3: C101.1, C102.1, C103.1, C105.1, C106.1, C107.1, C108.1, C109.1, C110.1, D104.2, D202.1, D204.1, D208.1, D212.1, D216.1, R206.1, R211.1, R216.1, R221.1, TP104.1, U103.1, U105.13, U106.1, U106.9, U106.24, U106.36, U106.48, U107.3
+BATT: D201.1, D205.1, D209.1, D213.1, D217.1, F101.2, K201.2, K201.3, K202.2, K203.2, K204.2, K205.2, P109.2, R101.1, R205.2, R209.2, R215.2, R219.2, TP101.1, U107.1
/ARM_LED: R103.2, U106.45
/BATT_MON: R101.2, R102.1, U106.10
/BUZZER: R105.2, R106.1, U106.14
/DISARM_LED: P107.1, U106.46
/RFM_DIO0: U105.14, U106.4
/RFM_DIO1: U105.15, U106.3
/RFM_DIO2: U105.16, U106.2
/RFM_DIO3: U105.11, U106.42
/RFM_DIO4: U105.12, U106.43
/RFM_DIO5: U105.7, U106.32
/RFM_MISO: U105.2, U106.40
/RFM_MOSI: U105.3, U106.41
/RFM_NSS: U105.5, U106.38
/RFM_RESET: U105.6, U106.33
/RFM_SCK: U105.4, U106.39
/SWDCLK: U103.4, U106.37
/SWDIO: U103.2, U106.34
/firing/CONT_CH1: D208.2, R212.1, TP205.1, U106.18
/firing/CONT_CH2: D216.2, R222.1, TP207.1, U106.17
/firing/CONT_CH3: D204.2, R207.1, TP204.1, U106.16
/firing/CONT_CH4: D212.2, R217.1, TP206.1, U106.15
/firing/FIRE_CH1: R213.2, R214.1, U106.30
/firing/FIRE_CH2: R223.2, R224.1, U106.29
/firing/FIRE_CH3: R208.2, R210.1, U106.28
/firing/FIRE_CH4: R218.2, R220.1, U106.27
/firing/FIRING_DIST: K201.4, K202.3, K203.3, K204.3, K205.3, R203.2, R204.1, TP201.1
/firing/RELAY_SENSE: D202.2, R203.1, TP203.1, U106.19
/firing/UPSTREAM_RELAY: R201.2, R202.2, TP202.1, U106.31
/nRST: C104.1, TP103.1, U103.10, U106.7
GND: C101.2, C102.2, C103.2, C104.2, C105.2, C106.2, C107.2, C108.2, C109.2, C110.2, C111.2, C112.2, D101.2, D103.2, D206.2, D210.2, D214.2, D218.2, P105.1, P111.2, P111.3, P111.4, P111.5, P203.1, P206.1, P209.1, P212.1, Q101.2, Q201.2, Q202.2, Q203.2, Q204.2, Q205.2, R102.2, R106.2, R107.2, R108.2, R109.2, R202.1, R204.2, R210.2, R214.2, R220.2, R224.2, TP102.1, U103.3, U103.5, U103.9, U105.1, U105.8, U105.10, U106.8, U106.23, U106.35, U106.44, U106.47, U107.2
unnamed: C111.1, R104.1, Y101.2
unnamed: C112.1, U106.5, Y101.1
unnamed: D101.1, F101.1, P105.2
unnamed: D103.1, P111.1, U105.9
unnamed: D104.1, R107.1
unnamed: D105.1, R108.1
unnamed: D105.2, U106.25
unnamed: D106.1, R109.1
unnamed: D106.2, U106.26
unnamed: D201.2, K201.1, Q201.3
unnamed: D205.2, K202.1, P201.1, Q202.3
unnamed: D206.1, K202.4, P203.2, R206.2, R207.2
unnamed: D209.2, K203.1, P204.1, Q203.3
unnamed: D210.1, K203.4, P206.2, R211.2, R212.2
unnamed: D213.2, K204.1, P207.1, Q204.3
unnamed: D214.1, K204.4, P209.2, R216.2, R217.2
unnamed: D217.2, K205.1, P210.1, Q205.3
unnamed: D218.1, K205.4, P212.2, R221.2, R222.2
unnamed: P107.2, R103.1
unnamed: P109.1, Q101.3
unnamed: P201.2, R205.1
unnamed: P204.2, R209.1
unnamed: P207.2, R215.1
unnamed: P210.2, R219.1
unnamed: Q101.1, R105.1
unnamed: Q201.1, R201.1
unnamed: Q202.1, R208.1
unnamed: Q203.1, R213.1
unnamed: Q204.1, R218.1
unnamed: Q205.1, R223.1
unnamed: R104.2, U106.6

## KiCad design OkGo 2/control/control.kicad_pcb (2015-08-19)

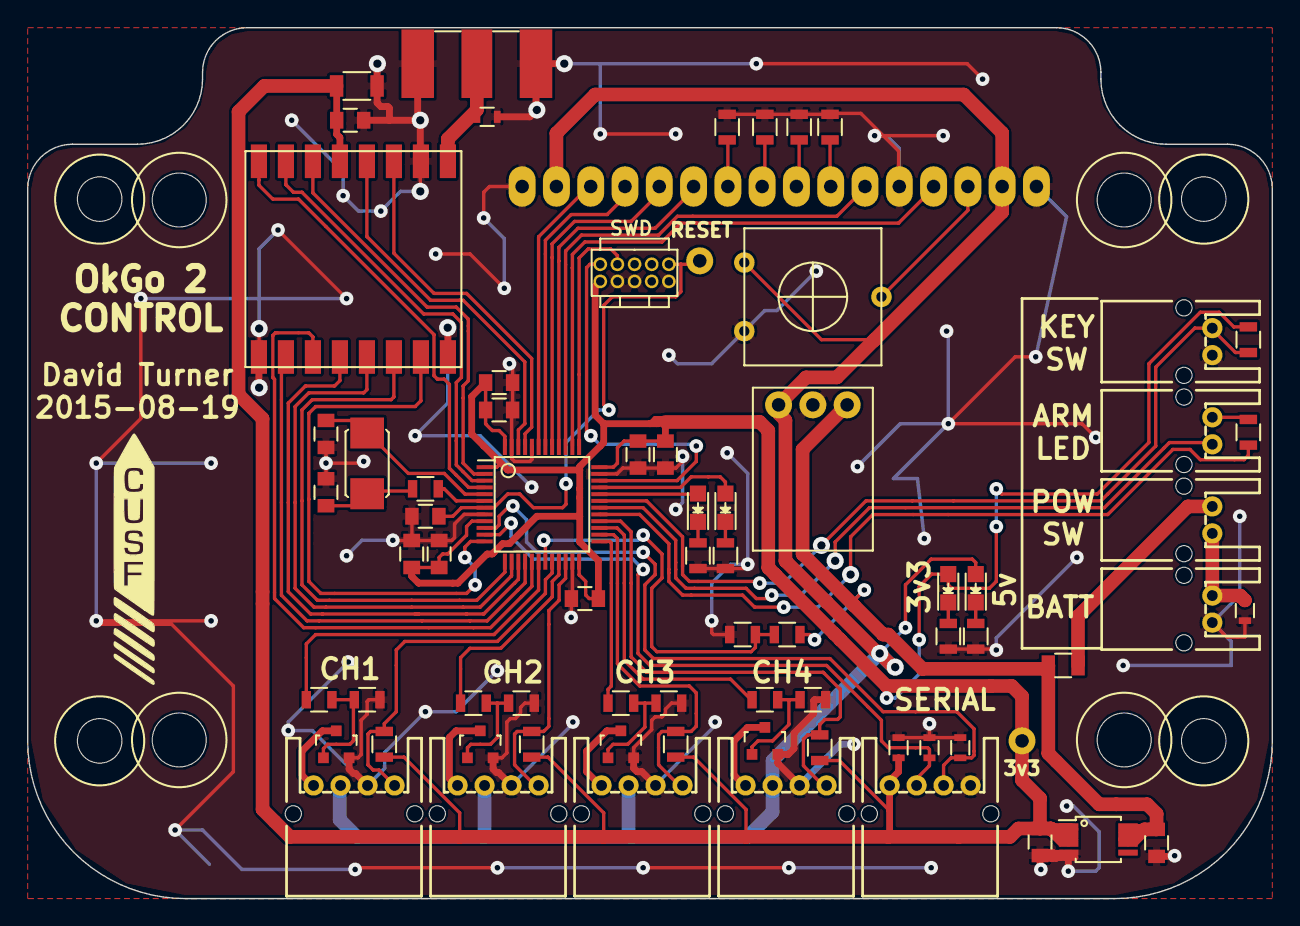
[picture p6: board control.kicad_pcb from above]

Board: 2 copper layers, 92.2 x 64.5 mm, 77 parts (1 on the bottom side), 64 nets.

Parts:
C101, C102, C104, C108, C112: 100n; C_0805
C103, C105: 4u7; C_0805
C106: 10n; C_0805
C107: 1u; C_0805
C109, C110: 15p; C_0805
C111: 100u; C_1206
C113, C114: 2u2; C_0805
D101, D103, D104, D105, D106: TVS_small; R_0603
D107, D110: RED; LED-0805
D108: GREEN; LED-0805
D109: YELLOW; LED-0805
F101: PTC; polyfuse0805
M3_MOUNT, M3_MOUNT#2, M3_MOUNT#3, M3_MOUNT#4: VAL**; M3_MOUNT
P102: KEYSW; JST-PA-2
P105: BATT; JST-PA-2
P106: ARM_LED; JST-PA-2
P108: SMA; SMA-142-0701-801
P110: POWER_SW; JST-PA-2
P111: SERIAL; JST-PA-4
P201: CH1; JST-PA-4
P202: CH2; JST-PA-4
P205: CH3; JST-PA-4
P206: CH4; JST-PA-4
Q201, Q202, Q203, Q204: BSS138BK; SOT-23
R101, R106, R107, R108, R109, R110, R205, R206, R211, R212: 10k; R_0805
R102: 100R; R_0805
R103: 75R; R_0805
R104: R_Small; R_0805
R105: 3k3; R_0805
R111, R112, R113: R; R_0805
R201, R202, R207, R208: 180R; R_0805
R203, R204, R209, R210: 100k; R_0805
RV101: 20k LIN; bourns3386G
TP101: nRST; TESTPOINT
TP102: 3v3; TESTPOINT
U101: SWD; FTSH-105-01-F-D-K
U102: STM32F071CBT6; LQFP48_ST
U103: pololu_S7V7F5; polulo_S7V7F5
U105: RFM95W
U106: LCD_HD44780; LCD_MC42004A6W_bare
U107: ADP3335; MSOP-8_3x3mm_Pitch0.65mm
Y101: 8MHz; XTAL50x32

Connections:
+3V3: C101.1, C102.1, C103.1, C104.1, C105.1, C106.1, C107.1, C111.2, C112.2, C114.1, D106.1, D107.2, P111.4, R101.1, R205.1, R206.1, R211.1, R212.1, TP102.1, U101.1, U102.1, U102.9, U102.24, U102.36, U102.48, U105.13, U107.1, U107.2, U107.3
+5V: D110.2, P201.3, P202.3, P205.3, P206.3, RV101.1, U103.3, U106.2, U106.15
+BATT: C113.1, F101.2, R105.1, U103.1, U107.6, U107.7, U107.8
/ARM_LED: R103.2, U102.29
/ARM_SW: P102.2, R101.2, U102.31
/BATT_MON: R105.2, R106.1, U102.19
/DISARM_LED: P106.1, U102.30
/LCD_DB4: U102.40, U106.11
/LCD_DB5: U102.41, U106.12
/LCD_DB6: U102.42, U106.13
/LCD_DB7: U102.43, U106.14
/LCD_E: U102.39, U106.6
/LCD_RS: U102.38, U106.4
/RFM_DIO0: U102.2, U105.14
/RFM_DIO1: U102.3, U105.15
/RFM_DIO2: U102.4, U105.16
/RFM_DIO3: U102.45, U105.11
/RFM_DIO4: U102.46, U105.12
/RFM_DIO5: U102.12, U105.7
/RFM_MISO: U102.16, U105.2
/RFM_MOSI: U102.17, U105.3
/RFM_NSS: U102.14, U105.5
/RFM_RESET: U102.13, U105.6
/RFM_SCK: U102.15, U105.4
/SWDCLK: U101.4, U102.37
/SWDIO: U101.2, U102.34
/controls/CH1_LED: R201.2, U102.18
/controls/CH1_SW: P201.1, R205.2, U102.20
/controls/CH2_LED: R202.2, U102.21
/controls/CH2_SW: P202.1, R206.2, U102.22
/controls/CH3_LED: R207.2, U102.25
/controls/CH3_SW: P205.1, R211.2, U102.26
/controls/CH4_LED: R208.2, U102.27
/controls/CH4_SW: P206.1, R212.2, U102.28
/nRST: C108.1, TP101.1, U101.10, U102.7
GND: C101.2, C102.2, C103.2, C104.2, C105.2, C106.2, C107.2, C108.2, C109.2, C110.2, C111.1, C112.1, C113.2, C114.2, D101.2, D103.1, D104.2, D105.2, D106.2, P102.1, P105.1, P108.2, P108.3, P108.4, P108.5, P111.1, P201.2, P202.2, P205.2, P206.2, Q201.2, Q202.2, Q203.2, Q204.2, R104.2, R106.2, R107.2, R108.2, R109.2, R110.2, R111.2, R112.2, R113.2, R203.2, R204.2, R209.2, R210.2, RV101.3, U101.3, U101.5, U101.9, U102.8, U102.23, U102.35, U102.44, U102.47, U103.2, U105.1, U105.8, U105.10, U106.1, U106.5, U106.16, U107.4
unnamed: C109.1, R102.2, Y101.2
unnamed: C110.1, U102.5, Y101.1
unnamed: D101.1, P105.2, P110.1
unnamed: D103.2, P108.1, U105.9
unnamed: D104.1, P111.2, U102.10
unnamed: D105.1, P111.3, U102.11
unnamed: D107.1, R104.1
unnamed: D108.1, R111.1
unnamed: D108.2, U102.33
unnamed: D109.1, R112.1
unnamed: D109.2, U102.32
unnamed: D110.1, R113.1
unnamed: F101.1, P110.2
unnamed: P106.2, R103.1
unnamed: P201.4, Q201.3
unnamed: P202.4, Q202.3
unnamed: P205.4, Q203.3
unnamed: P206.4, Q204.3
unnamed: Q201.1, R201.1, R203.1
unnamed: Q202.1, R202.1, R204.1
unnamed: Q203.1, R207.1, R209.1
unnamed: Q204.1, R208.1, R210.1
unnamed: R102.1, U102.6
unnamed: R107.1, U106.10
unnamed: R108.1, U106.9
unnamed: R109.1, U106.8
unnamed: R110.1, U106.7
unnamed: RV101.2, U106.3

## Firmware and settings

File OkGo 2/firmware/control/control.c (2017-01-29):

#include <stdint.h>
#include <stdbool.h>

#include <libopencm3/stm32/gpio.h>
#include <libopencm3/stm32/rcc.h>

/* Common includes */
#include "rfm95w.h"
#include "utils.h"

/* control-specific includes */
#include "control.h"
#include "control_radio.h"
#include "control_pins.h"
#include "display.h"
#include "adc.h"
#include "splash.h"

/* Configuration constants */
const uint16_t SLOW_PACKET_DELAY = 1000; /* delay in ms */
const uint16_t FAST_PACKET_DELAY = 250; /* delay in ms */
const uint32_t PACKET_DROP_DELAY = 2000;
const uint8_t RADIO_POWER_DBM = 10; /* Radio tx power in dBm */
const uint8_t MAX_RESISTANCE = 50; /* Max R in ohms of device otherwise CERR */

/* Internal functions */

/* Initialisation including clocks, pins, radio, state, ADCs */
void control_init(control_state *state, control_radio_state *radio_state);

/* Convert a channel status enum into a string and print to LCD */
void control_display_ch_status(uint8_t ch_status, bool remote_fire);

/* Display a continuity resistance to the LCD */
void control_display_ch_cont(uint8_t cont, uint8_t ch_status);

/* Update display from local state */
void control_display_update(control_state *state,
                            control_radio_state *radio_state);

void control_init(control_state *state, control_radio_state *radio_state)
{
    /* Initialise local state variables */
    state->armed = false;
    state->centre_frf = FRF_868;
    state->ch1_status = CH_STATUS_OK;
    state->ch2_status = CH_STATUS_OK;
    state->ch3_status = CH_STATUS_OK;
    state->ch4_status = CH_STATUS_OK;

    /* Setup crystal oscillator and systick */
    rcc_clock_setup_in_hsi_out_48mhz();
    systick_init();

    /* Clock GPIOs, set pin modes */
    control_pins_init();

    /* Initialise radio and radio state */
    control_radio_init(radio_state);
    rfm_setfreq(state->centre_frf);
    rfm_setpower(RADIO_POWER_DBM);

    /* ADC Setup: Clock periph, run init. Pins done in control_pins */
    rcc_periph_clock_enable(RCC_ADC);
    adc_init();

    /* Initialise display */
    lcd_init();
}

/* Display a continuity resistance to the LCD */
void control_display_ch_status(uint8_t ch_status, bool remote_fire)
{
    if(remote_fire)
    {
        lcd_puts("FIRE ");
        return;
    }

    switch(ch_status)
    {
        case CH_STATUS_OK:
            lcd_puts(" OK  ");
            break;
        case CH_STATUS_CONT_ERR:
            lcd_puts(" ERR ");
            break;
        case CH_STATUS_FIRE:
            /* We are requesting fire but remote refuses/ignores */
            lcd_puts(" NO  ");
            break;
        default:
            lcd_puts("     ");
    }
}

/* Display a continuity resistance to the LCD */
void control_display_ch_cont(uint8_t cont, uint8_t ch_status)
{
    /* Don't display invalid continuities for firing channels */
    if(ch_status == CH_STATUS_FIRE)
    {
        lcd_puts("     ");
        return;
    }

    if(cont == 255)
    {
        /* 255 is a magic value meaning open */
        lcd_puts("  ");
        lcd_putc(0b11110011);
    }
    else if(cont == 254)
        /* 254 is a magic value meaning >255 but not open */
        lcd_puts(" hi");
    else
    {
        lcd_putc('0' + cont / 100);
        lcd_putc('0' + (cont / 10) % 10);
        lcd_putc('0' + cont % 10);
    }
    lcd_putc(0b11110100); /* Character code for ohms */
    lcd_putc(' ');
}

/* Update display from local state */
void control_display_update(control_state *state,
                            control_radio_state *radio_state)
{
    /* Display format (link):
     * ######################
     * #3.7V  DISARM SIG:99%#
     * #12.2V DISARM SIG:80%#
     * #002R      255R 000R #
     * # OK  FIRE ERR   OK  #
     * ######################
     *
     * Display format (no link):
     * ######################
     * #3.7V  DISARM SIG:0%V#
     * #      NO LINK!      #
     * #002R      255R 000R #
     * # OK  FIRE ERR   OK  #
     * ######################
     */
    uint32_t adc_val;
    uint32_t control_batt_voltage;
    adc_val = adc_read(ADC_CH_CTRL_BATT); /* Read raw value */
    adc_val = adc_to_millivolts(adc_val); /* Convert to millivolts */
    /* Batt voltage comes via a 3k3 over 10k potential divider such that
     * V = Vbatt * 10/13.3
     * Vbatt = V * 133/100 */
    control_batt_voltage = adc_val * 133 / 100;
    /* We will round to tenths of a volt, AKA 100 millivolts
     * This bodge means the later implicit truncation acts like a proper round
     * Ignition is sent over pre-rounded so we don't need to do this for it */
    if((control_batt_voltage / 10) % 10 >= 5)
        control_batt_voltage += 10;

    /* Control battery voltage */
    lcd_cursor_pos(0, 0);
    lcd_putc('0' + control_batt_voltage / 1000);
    lcd_putc('.');
    lcd_putc('0' + (control_batt_voltage / 100) % 10);
    lcd_puts("V  ");

    /* Control state */
    lcd_cursor_pos(0, 6);
    if(state->armed)
        lcd_puts("ARMED  ");
    else
        lcd_puts("DISARM ");

    /* Control signal level */
    lcd_cursor_pos(0, 13);
    lcd_puts("SIG:");
    lcd_putc('0' + radio_state->packet_rssi / 10);
    lcd_putc('0' + radio_state->packet_rssi % 10);
    lcd_putc('%');

    /* Ignition's row: */
    lcd_cursor_pos(1, 0);
    if(!radio_state->lost_link)
    {
        /* Battery voltage */
        lcd_putc('0' + radio_state->rx_voltage / 100);
        lcd_putc('0' + (radio_state->rx_voltage / 10) % 10);
        lcd_putc('.');
        lcd_putc('0' + radio_state->rx_voltage % 10);
        lcd_puts("V ");

        /* State: */
        if(radio_state->rx_status & (0b11100000))
            lcd_puts("ERROR  ");
        else
            if(radio_state->rx_status & (1<<4))
                lcd_puts("ARMED  ");
            else
                lcd_puts("DISARM ");

        /* Signal level */
        lcd_puts("SIG:");
        lcd_putc('0' + radio_state->rx_rssi / 10);
        lcd_putc('0' + radio_state->rx_rssi % 10);
        lcd_putc('%');
    }
    else
        lcd_puts("      NO LINK!      ");


    /* Channel continuities */
    lcd_cursor_pos(2, 0);
    if(!radio_state->lost_link)
    {
        control_display_ch_cont(radio_state->rx_cont1, state->ch1_status);
        control_display_ch_cont(radio_state->rx_cont2, state->ch2_status);
        control_display_ch_cont(radio_state->rx_cont3, state->ch3_status);
        control_display_ch_cont(radio_state->rx_cont4, state->ch4_status);
    }
    else
        lcd_puts("                    ");

    /* Control channel status */
    lcd_cursor_pos(3, 0);
    control_display_ch_status(state->ch1_status, radio_state->rx_status&0x01);
    control_display_ch_status(state->ch2_status, radio_state->rx_status&0x02);
    control_display_ch_status(state->ch3_status, radio_state->rx_status&0x04);
    control_display_ch_status(state->ch4_status, radio_state->rx_status&0x08);

}

int main(void)
{
    control_state state;
    control_radio_state radio_state;
    uint32_t loop_timer;
    uint32_t last_packet = 0;

    control_init(&state, &radio_state);

    splash();

    /* Default: deafen */
    state.beep_volume = 3;
    if(!gpio_get_bool(SW_CH1_PORT, SW_CH1))
        state.beep_volume = 0; /* off */
    if(!gpio_get_bool(SW_CH2_PORT, SW_CH2))
        state.beep_volume = 1; /* low */
    if(!gpio_get_bool(SW_CH3_PORT, SW_CH3))
        state.beep_volume = 2; /* med */
    if(!gpio_get_bool(SW_CH4_PORT, SW_CH4))
        state.beep_volume = 3; /* high */

    gpio_set(LED_GREEN_PORT, LED_GREEN);
    gpio_clear(LED_YELLOW_PORT, LED_YELLOW);

    loop_timer = get_millis();
    while(1)
    {
        /* Arming status */
        state.armed = !gpio_get_bool(SW_KEY_PORT, SW_KEY);
        gpio_set_bool(LED_ARM_PORT, LED_ARM, state.armed);
        gpio_set_bool(LED_DISARM_PORT, LED_DISARM, !(state.armed));

        /* Start with channels okay and un-firing */
        state.ch1_status = CH_STATUS_OK;
        state.ch2_status = CH_STATUS_OK;
        state.ch3_status = CH_STATUS_OK;
        state.ch4_status = CH_STATUS_OK;

        /* Detect continuity errors */
        if(!radio_state.lost_link)
        {
            if(radio_state.rx_cont1 > MAX_RESISTANCE)
                state.ch1_status = CH_STATUS_CONT_ERR;
            if(radio_state.rx_cont2 > MAX_RESISTANCE)
                state.ch2_status = CH_STATUS_CONT_ERR;
            if(radio_state.rx_cont3 > MAX_RESISTANCE)
                state.ch3_status = CH_STATUS_CONT_ERR;
            if(radio_state.rx_cont4 > MAX_RESISTANCE)
                state.ch4_status = CH_STATUS_CONT_ERR;
        }

        /* Detect firing state */
        if(state.armed)
        {
            if(!gpio_get_bool(SW_CH1_PORT, SW_CH1))
                state.ch1_status = CH_STATUS_FIRE;
            if(!gpio_get_bool(SW_CH2_PORT, SW_CH2))
                state.ch2_status = CH_STATUS_FIRE;
            if(!gpio_get_bool(SW_CH3_PORT, SW_CH3))
                state.ch3_status = CH_STATUS_FIRE;
            if(!gpio_get_bool(SW_CH4_PORT, SW_CH4))
                state.ch4_status = CH_STATUS_FIRE;
        }

        /* Set channel LEDs based on firing/cont and armed status */
        gpio_set_bool(LED_CH1_PORT, LED_CH1,
                      state.armed && (state.ch1_status == CH_STATUS_OK));
        gpio_set_bool(LED_CH1_PORT, LED_CH2,
                      state.armed && (state.ch2_status == CH_STATUS_OK));
        gpio_set_bool(LED_CH1_PORT, LED_CH3,
                      state.armed && (state.ch3_status == CH_STATUS_OK));
        gpio_set_bool(LED_CH1_PORT, LED_CH4,
                      state.armed && (state.ch4_status == CH_STATUS_OK));

        /* Do TX */
        gpio_set(LED_YELLOW_PORT, LED_YELLOW);
        control_radio_transmit(&state, &radio_state);
        gpio_clear(LED_YELLOW_PORT, LED_YELLOW);

        /* Setup receiver */
        rfm_receive_async(17);

        /* Update display */
        control_display_update(&state, &radio_state);

        /* Delay to correctly set loop timing */
        if(state.armed)
            while((get_millis() - loop_timer) < FAST_PACKET_DELAY);
        else
            while((get_millis() - loop_timer) < SLOW_PACKET_DELAY);
        loop_timer = get_millis();

        /* Attempt receive (used in next cycle before delay) */
        control_radio_receive_async(&radio_state);

        if(radio_state.valid_rx)
            last_packet = get_millis();
        if((get_millis() - last_packet) > PACKET_DROP_DELAY)
            radio_state.lost_link = true;
        else
            radio_state.lost_link = false;

        gpio_toggle(LED_GREEN_PORT, LED_GREEN);
    }

    return 0;
}

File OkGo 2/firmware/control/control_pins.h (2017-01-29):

#ifndef CONTROL_PINS_H
#define CONTROL_PINS_H

#include <libopencm3/stm32/gpio.h>

/* Clock GPIOs, set pin modes (except radio and display) */
void control_pins_init(void);

/* LEDs */
#define LED_GREEN       GPIO12
#define LED_GREEN_PORT  GPIOA
#define LED_YELLOW      GPIO11
#define LED_YELLOW_PORT GPIOA

#define LED_ARM         GPIO8
#define LED_ARM_PORT    GPIOA
#define LED_DISARM      GPIO9
#define LED_DISARM_PORT GPIOA

/* Keyswitch */
#define SW_KEY          GPIO10
#define SW_KEY_PORT     GPIOA

/* Channels - switches and LEDs */
#define LED_CH1         GPIO0
#define LED_CH1_PORT    GPIOB
#define LED_CH2         GPIO10
#define LED_CH2_PORT    GPIOB
#define LED_CH3         GPIO12
#define LED_CH3_PORT    GPIOB
#define LED_CH4         GPIO14
#define LED_CH4_PORT    GPIOB

#define SW_CH1          GPIO2
#define SW_CH1_PORT     GPIOB
#define SW_CH2          GPIO11
#define SW_CH2_PORT     GPIOB
#define SW_CH3          GPIO13
#define SW_CH3_PORT     GPIOB
#define SW_CH4          GPIO15
#define SW_CH4_PORT     GPIOB

/* LCD */
#define LCD_RS          GPIO15
#define LCD_RS_PORT     GPIOA
#define LCD_E           GPIO3
#define LCD_E_PORT      GPIOB
#define LCD_DB4         GPIO4
#define LCD_DB4_PORT    GPIOB
#define LCD_DB5         GPIO5
#define LCD_DB5_PORT    GPIOB
#define LCD_DB6         GPIO6
#define LCD_DB6_PORT    GPIOB
#define LCD_DB7         GPIO7
#define LCD_DB7_PORT    GPIOB

/* Radio */
#define RFM_NSS         GPIO4
#define RFM_NSS_PORT    GPIOA
#define RFM_SCK         GPIO5
#define RFM_SCK_PORT    GPIOA
#define RFM_MISO        GPIO6
#define RFM_MISO_PORT   GPIOA
#define RFM_MOSI        GPIO7
#define RFM_MOSI_PORT   GPIOA
#define RFM_RESET       GPIO3
#define RFM_RESET_PORT  GPIOA
#define RFM_DIO0        GPIO13
#define RFM_DIO0_PORT   GPIOC
#define RFM_DIO1        GPIO14
#define RFM_DIO1_PORT   GPIOC
#define RFM_DIO2        GPIO15
#define RFM_DIO2_PORT   GPIOC
#define RFM_DIO3        GPIO8
#define RFM_DIO3_PORT   GPIOB
#define RFM_DIO4        GPIO9
#define RFM_DIO4_PORT   GPIOB
#define RFM_DIO5        GPIO2
#define RFM_DIO5_PORT   GPIOA

/* Analog pins */
#define BATT_MON        GPIO1
#define BATT_MON_PORT   GPIOB

#endif

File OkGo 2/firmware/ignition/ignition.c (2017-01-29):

#include <stdint.h>
#include <stdbool.h>

#include <libopencm3/stm32/gpio.h>
#include <libopencm3/stm32/rcc.h>

#include "rfm95w.h"
#include "utils.h"
#include "adc.h"

#include "ignition.h"
#include "ignition_pins.h"
#include "ignition_radio.h"

const uint8_t RADIO_POWER_DBM = 10; /* Radio tx power in dBm */
const uint32_t PACKET_DROP_DELAY = 5000; /* Drop delay in ms */

/* Internal functions */
void ignition_init(ignition_state *state, ignition_radio_state *radio_state);

/* Do beeping */
void do_beep(ignition_state *state);

void ignition_init(ignition_state *state, ignition_radio_state *radio_state)
{
    /* Initialise local state variables */
    state->armed = false;
    state->fire_ch1 = false;
    state->fire_ch2 = false;
    state->fire_ch3 = false;
    state->fire_ch4 = false;
    state->centre_frf = FRF_868;
    state->beep_start = 0;
    state->beep_volume = 2;

    /* Setup crystal oscillator and systick */
    rcc_clock_setup_in_hsi_out_48mhz();
    systick_init();

    /* Clock GPIOs, set pin modes */
    ignition_pins_init();

    /* Initialise radio and local state variables, read stored config*/
    ignition_radio_init(radio_state);
    rfm_setfreq(state->centre_frf);
    rfm_setpower(RADIO_POWER_DBM);

    /* ADC Setup: Clock periph, run init. Pins done in ignition_pins */
    rcc_periph_clock_enable(RCC_ADC);
    adc_init();
}

/* Do beeping */
void do_beep(ignition_state *state)
{
    uint32_t beep_period;
    uint32_t beep_len;

    if(state->fire_ch1 || state->fire_ch2 || state->fire_ch3 ||
       state->fire_ch4)
    {
        beep_period = 200; /* fire beep period */
        beep_len = 50; /* fire beep length */
    }
    else if(state->armed)
    {
        beep_period = 500; /* armed beep period */
        beep_len = 250; /* armed beep length */
    }
    else
    {
        beep_period = 1000; /* disarmed beep period */
        beep_len = 50; /* disarmed beep len */
    }

    if((get_millis() - state->beep_start) > beep_period)
    {
        /* Start a new beep with the high cycle */
        state->beep_start = get_millis();
        switch(state->beep_volume)
        {
            case 0:
                ignition_buzzer_set(0); /* No beep */
                break;
            case 1:
                ignition_buzzer_set(94); /* Low beep */
                break;
            case 3:
                ignition_buzzer_set(255); /* Deafening beep */
                break;
            default:
                ignition_buzzer_set(112); /* Medium beep */
                break;
        }
    }
    else if((get_millis() - state->beep_start) > beep_len)
        /* Do the low cycle of the beep */
        ignition_buzzer_set(0); /* off */
}

int main(void)
{
    ignition_state state;
    ignition_radio_state radio_state;
    uint32_t last_packet = 0;

    ignition_init(&state, &radio_state);

    gpio_set(LED_GREEN_PORT, LED_GREEN);
    gpio_clear(LED_YELLOW_PORT, LED_YELLOW);

    rfm_receive_async(11);

    while(1)
    {
        if(rfm_packet_waiting())
        {
            ignition_radio_receive_async(&radio_state);
            if(radio_state.valid_rx)
            {
                last_packet = get_millis();
                state.armed = radio_state.command & (1<<4);
                state.beep_volume = (radio_state.command >> 5) & 0x07;
                if(state.armed)
                {
                    state.fire_ch1 = radio_state.command & (1<<0);
                    state.fire_ch2 = radio_state.command & (1<<1);
                    state.fire_ch3 = radio_state.command & (1<<2);
                    state.fire_ch4 = radio_state.command & (1<<3);
                }
                else
                {
                    state.fire_ch1 = false;
                    state.fire_ch2 = false;
                    state.fire_ch3 = false;
                    state.fire_ch4 = false;
                }
            }
            delay_ms(10);
            ignition_radio_transmit(&state, &radio_state);
            rfm_receive_async(11);
            gpio_toggle(LED_GREEN_PORT, LED_GREEN);
            gpio_toggle(LED_YELLOW_PORT, LED_YELLOW);
        }

        if(state.armed && !radio_state.lost_link)
        {
            gpio_set(LED_ARM_PORT, LED_ARM);
            gpio_clear(LED_DISARM_PORT, LED_DISARM);
            gpio_set(UPSTREAM_RELAY_PORT, UPSTREAM_RELAY);
            gpio_set_bool(FIRE_CH1_PORT, FIRE_CH1, state.fire_ch1);
            gpio_set_bool(FIRE_CH2_PORT, FIRE_CH2, state.fire_ch2);
            gpio_set_bool(FIRE_CH3_PORT, FIRE_CH3, state.fire_ch3);
            gpio_set_bool(FIRE_CH4_PORT, FIRE_CH4, state.fire_ch4);
        }
        else
        {
            gpio_clear(LED_ARM_PORT, LED_ARM);
            gpio_set(LED_DISARM_PORT, LED_DISARM);
            gpio_clear(UPSTREAM_RELAY_PORT, UPSTREAM_RELAY);
            gpio_clear(FIRE_CH1_PORT, FIRE_CH1);
            gpio_clear(FIRE_CH2_PORT, FIRE_CH2);
            gpio_clear(FIRE_CH3_PORT, FIRE_CH3);
            gpio_clear(FIRE_CH4_PORT, FIRE_CH4);
        }

        if((get_millis() - last_packet) > PACKET_DROP_DELAY)
            radio_state.lost_link = true;
        else
            radio_state.lost_link = false;

        if(radio_state.lost_link)
        {
            gpio_clear(LED_ARM_PORT, LED_ARM);
            gpio_set(LED_DISARM_PORT, LED_DISARM);
            gpio_clear(UPSTREAM_RELAY_PORT, UPSTREAM_RELAY);
            gpio_clear(FIRE_CH1_PORT, FIRE_CH1);
            gpio_clear(FIRE_CH2_PORT, FIRE_CH2);
            gpio_clear(FIRE_CH3_PORT, FIRE_CH3);
            gpio_clear(FIRE_CH4_PORT, FIRE_CH4);
        }

        do_beep(&state);
    }


    return 0;
}

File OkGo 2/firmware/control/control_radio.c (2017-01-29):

#include <stdbool.h>
#include <stdint.h>
#include <string.h>

#include <libopencm3/stm32/gpio.h>
#include <libopencm3/stm32/rcc.h>
#include <libopencm3/stm32/spi.h>

#include "control_pins.h"
#include "control_radio.h"
#include "rfm95w.h"
#include "control.h"
#include "hmac.h"
#include "key.h"

/* Setup the SPI peripheral and call the RGM95W initialization procedure.
 * Also initialise all the state variables to sensible defaults */
void control_radio_init(control_radio_state *radio_state)
{
    /* Clock SPI1 peripheral and setup GPIOs appropriately:
     * NSS, SCK, MOSI, RESET are outputs,
     * MISO is input.
     * SPI setup is done in rfm95w.c */
    rcc_periph_clock_enable(RCC_SPI1);

    /* Make sure NSS doesn't blip when we enable it: */
    gpio_set(RFM_NSS_PORT, RFM_NSS);
    gpio_mode_setup(RFM_NSS_PORT, GPIO_MODE_OUTPUT, GPIO_PUPD_NONE, RFM_NSS);
    gpio_mode_setup(RFM_SCK_PORT, GPIO_MODE_AF, GPIO_PUPD_NONE, RFM_SCK);
    gpio_mode_setup(RFM_MOSI_PORT, GPIO_MODE_AF, GPIO_PUPD_NONE, RFM_MOSI);
    gpio_mode_setup(RFM_MISO_PORT, GPIO_MODE_AF, GPIO_PUPD_NONE, RFM_MISO);
    gpio_set_af(RFM_SCK_PORT, GPIO_AF0, RFM_SCK);
    gpio_set_af(RFM_MOSI_PORT, GPIO_AF0, RFM_MOSI);
    gpio_set_af(RFM_MISO_PORT, GPIO_AF0, RFM_MISO);

    /* Bring the radio out of reset: rfm_init will wait for it to warm up */
    /*gpio_mode_setup(RFM_RESET_PORT, GPIO_MODE_OUTPUT, GPIO_PUPD_NONE,
                    RFM_RESET);*/
    /*gpio_set(RFM_RESET_PORT, RFM_RESET);*/
    /* By default leave RFM_RESET high-Z as requested by datasheet */

    /* Run RFM95W initialization */
    rfm_initialise(SPI1, RFM_NSS_PORT, RFM_NSS);

    /* Setup state variables to sensible defaults */
    radio_state->valid_rx = false;
    radio_state->lost_link = true;
    radio_state->rx_rssi = 0;
    radio_state->rx_voltage = 0;
    radio_state->rx_status = 0;
    radio_state->rx_cont1 = 0;
    radio_state->rx_cont2 = 0;
    radio_state->rx_cont3 = 0;
    radio_state->rx_cont4 = 0;
    radio_state->packet_rssi = 0;
}

/* Transmit a packet to ignition based on the contents of state */
void control_radio_transmit(control_state *state, control_radio_state *radio_state)
{
    uint8_t buf[11];
    uint8_t command = 0;

    (void)radio_state; /* Might use this later for a tx ID */

    command |= state->beep_volume << 5;
    command |= state->armed << 4;
    command |= (state->ch4_status == CH_STATUS_FIRE) << 3;
    command |= (state->ch3_status == CH_STATUS_FIRE) << 2;
    command |= (state->ch2_status == CH_STATUS_FIRE) << 1;
    command |= (state->ch1_status == CH_STATUS_FIRE);
    buf[0] = command;

    /* Generate message HMAC signature */
    hmac_md5_80(buf, 1, key, key_len, buf + 1);

    rfm_transmit(buf, 11);
}

/* Initiate packet reception and block until a packet is received */
void control_radio_receive_blocking(control_radio_state *radio_state)
{
    uint8_t rx_buf[17];

    rfm_receive(rx_buf, 17);
    control_radio_parse_packet(radio_state, rx_buf, 17);
    radio_state->packet_rssi = rfm_getrssi();
}

/* Retrieve and parse a packet received in async receive */
void control_radio_receive_async(control_radio_state *radio_state)
{
    uint8_t rx_buf[17];

    if(rfm_packet_retrieve(rx_buf, 17))
        control_radio_parse_packet(radio_state, rx_buf, 17);
    else
        radio_state->valid_rx = false;
    radio_state->packet_rssi = rfm_getrssi();
}

/* Parse a received radio packet and fill in the received packet datastore */
void control_radio_parse_packet(control_radio_state *radio_state, uint8_t *buf,
                                uint8_t len)
{
    uint8_t hmac[10];

    if(len != 17)
    {
        /* Invalid packet! */
        radio_state->valid_rx = false;
        return;
    }

    /* Check message HMAC signature.  Do this before unloading the rest of the
     * buffer so that we can still display the old data after dumping an
     * invalid packet */

    hmac_md5_80(buf, 7, key, key_len, hmac);
    if(memcmp(hmac, buf + 7, 10) == 0)
        radio_state->valid_rx = true; /* Good HMAC */
    else
    {
        radio_state->valid_rx = false; /* Invalid HMAC */
        return;
    }

    radio_state->rx_rssi = buf[0];
    radio_state->rx_voltage = buf[1];
    radio_state->rx_status = buf[2];
    radio_state->rx_cont1 = buf[3];
    radio_state->rx_cont2 = buf[4];
    radio_state->rx_cont3 = buf[5];
    radio_state->rx_cont4 = buf[6];

}

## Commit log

2012-11-25 Initial schematic commit
    [OkGo.sch]
2012-11-25 Finished first rev of schematic
    [OkGo.sch]
2012-11-25 Added connectors on firing/oxid loads
    [OkGo.sch]
2012-11-25 Added test and armed LEDs
    [OkGo.sch]
2012-11-25 Added firing box armed LED
    [OkGo.sch]
2012-11-25 Added handy schematic labels
    [OkGo.sch]
2012-11-25 Added a few farnell parts
    [OkGo.sch]
2012-11-26 Updated schematic to reflect ordered parts
    [OkGo.sch]
2012-11-26 Made schematic a little prettier
    [OkGo.sch]
2014-03-12 Added low oxid channel to schematic
    [OkGo.sch]
2014-03-12 Annotated schematic
    [OkGo.sch]
2014-03-13 New wiring layout on relay coils
    [OkGo.sch]
2015-05-10 Introducing OkGo 2 vague ideas outline.
    [OkGo.sch]
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2015-05-24 Control schematic except final pin assignment
    [control.sch]
2015-05-24 Start on ignition except firing/continuity things.
    [ignition.sch]
2015-05-25 Removed RFM GPIOs, added control LCD, removed LEDs
    [control.sch, ignition.sch]
2015-07-06 Updated schematics to new KiCAD
    [control.sch, ignition.sch]
2015-07-07 Removed SPI pins from STM32 pinout.
    Made them generic pins for more flexibility and less weirdness. Resolves #1.
    [control.sch, ignition.sch]
2015-07-08 Specced some parts on ignition schematic
    [ignition.sch]
2015-07-08 Added ESD suppression, resolves #13
    Also removed redundant pulldowns on firing channels.
    [control.sch, ignition.sch]
2015-07-08 Upstream relay, hierarchical sheets, local labels
    * Added upstream failsafe relay and stuck relay sensing
    * Moved out firing circuits to a separate sub-sheet below control
    * Converted all global labels to local labels
    * Fixed typo in naming of nRST on control sheet
    Resolves #12.
    [control.sch, firing.sch, ignition.sch]
2015-07-08 Connected nRST on ignition, fixes #10
    [ignition.sch]
2015-07-08 Removed pin labels from TVS
    [control.sch, ignition.sch]
2015-07-08 Test points. Resolves #14
    [control.sch, firing.sch, ignition.sch]
2015-07-08 Moved xtal drive resistors. Fixes #15
    [control.sch, ignition.sch]
2015-07-08 Specced/valued/footprinted a lot of parts
    [control.sch, firing.sch, ignition.sch]
2015-07-16 Lots and lots of part selections and small mods
    [control.sch, controls.sch, firing.sch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]
2015-07-16 New power buttons and arm/disarm LED
    [control.sch, controls.sch, firing.sch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]
2015-07-16 Changed and moved firing LEDs
    [firing.sch]
2015-07-18 Lots of footprinting.
    [control.sch, controls.sch, firing.sch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]
2015-07-18 Finished footprinting control, #7
    [control.sch, controls.sch]
2015-07-18 Footprinting on ignition + TPs
    [control.sch, firing.sch, ignition.sch]
2015-07-18 Flyback diodes, fixes #18
    [firing.sch, ignition.sch]
2015-07-18 Lots more footprinting, mostly done.
    [control.sch, firing.sch, ignition.sch]
2015-07-18 Non-handsoldering footprints, fixes #17
    [control.sch, controls.sch, firing.sch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]
2015-07-20 First layout of control
    [control.kicad_pcb, control.sch, controls.sch]
2015-07-28 experimental routing of some of control
    [control.kicad_pcb]
2015-07-28 4-bit LCD, pulldowns, 2-pin bicolour ARM LED
    [control.kicad_pcb, control.sch, controls.sch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]
2015-07-28 Finished demo-route of control
    [control.kicad_pcb, control.sch, controls.sch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]
2015-07-28 Fixed SOD123 footprint
2015-07-29 Added serial interface, resolves #19
    [control.kicad_pcb, control.sch, controls.sch]
2015-08-01 Revised control board outline
    [control-r1.kicad_pcb, control.kicad_pcb]
2015-08-02 2nd route of control, sans cleaning and checking
    [control.kicad_pcb, control.sch, controls.sch]
2015-08-07 Footprinting, rockers
    [control.sch, firing.sch, ignition.sch]
2015-08-11 minor schematic changes
    [firing.sch, ignition.sch]
2015-08-11 ignition part arranging, chose case
    [ignition.kicad_pcb]
2015-08-11 ignition; first attempt at placement
    [firing.sch, ignition.kicad_pcb, ignition.sch]
2015-08-12 ignition test routing somewhat done
    [firing.sch, ignition.kicad_pcb]
2015-08-13 Provisional first place+pinassign+route of ignition
    [control.kicad_pcb, ignition.kicad_pcb, ignition.sch]
2015-08-13 Second route of ignition
    [ignition.kicad_pcb, ignition.sch]
2015-08-14 Fixed #28, fixed #24, general tidying
    [control.kicad_pcb, firing.sch, ignition.kicad_pcb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]
2015-08-14 Fixed #28 on control
    [control.kicad_pcb]
2015-08-14 Tidied control 3v3,5 fixes #38
    [control.kicad_pcb]
2015-08-15 Fixes #22
    [ignition.kicad_pcb]
2015-08-17 LiPo cable tie holes, resolves #26
    [ignition.kicad_pcb]
2015-08-17 Moved control SWD, resolves #29
    [control.kicad_pcb]
2015-08-17 Changed SMA-F part
    [control.sch, ignition.sch]
2015-08-18 Corrected a bunch of footprints, see #9
    [control.kicad_pcb, control.sch, ignition.kicad_pcb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]
2015-08-18 More footprints, partial #9
    [control.kicad_pcb, control.sch, ignition.kicad_pcb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]
2015-08-18 Penultimate footprinting, partial #9
    [control.kicad_pcb, firing.sch, ignition.kicad_pcb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]
2015-08-18 Finished footprinting, resolves #9
    [control.kicad_pcb, control.sch, ignition.kicad_pcb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]
2015-08-18 Improved layout of control reg, fixes #41
    [control.kicad_pcb]
2015-08-19 Chunkied vias, rerouted some bits, resolves #36
    [control.kicad_pcb, ignition.kicad_pcb]
2015-08-19 Tidied control except cusf logo, partial #30
    [control.kicad_pcb]
2015-08-19 Control is photo-ready. Resolves #30
    [control.kicad_pcb]
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2015-08-19 Fixed weird wayward ground stitching
    [control.kicad_pcb]
2015-08-19 Updated control placement to make adam happy
    [control.kicad_pcb]
2015-08-19 Added LEDs to control
    [control-B_Cu.gbl, control-B_Mask.gbs, control-B_SilkS.gbo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]
2015-08-19 Added LEDs to ignition
    [firing.sch, ignition.kicad_pcb, ignition.sch]
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2015-08-19 Add 3v3 TP label on control, fix silk width
    [control.kicad_pcb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]
2015-08-19 Ctrl: New 5V reg, more ground stitching
    [control-B_Cu.gbl, control-B_Mask.gbs, control-B_SilkS.gbo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]
2015-08-19 Ctrl: Little capacitor wiggle
    [control-B_Cu.gbl, control-B_Mask.gbs, control-B_SilkS.gbo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]
2015-08-20 Ignition: Tidying, GND stitching, finishing
    [ignition-B_Cu.gbl, ignition-B_Mask.gbs, ignition-B_SilkS.gbo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]
2015-08-20 Fixed stitching derp. resolves #31
    [ignition-B_Cu.gbl, ignition-B_Mask.gbs, ignition-B_SilkS.gbo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]
2015-08-20 Fixed derped drill file
    [ignition-B_Cu.gbl, ignition-B_Mask.gbs, ignition-B_SilkS.gbo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]
2015-08-20 Moved vias from under fuse f/p
    [ignition-B_Cu.gbl, ignition-B_Mask.gbs, ignition-B_SilkS.gbo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]
2015-08-20 Unmask bottom tracks on ignition
    [ignition-B_Cu.gbl, ignition-B_Mask.gbs, ignition-B_SilkS.gbo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]
2015-08-20 fix silk label cont ch4->cont ch3
    [ignition.kicad_pcb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]
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2015-08-27 Swapped ignition debug LED colours, fixes #46
    [ignition.sch]
2015-08-29 CAM and paste-stencil files
    [control-F_Paste.dxf, ignition-F_Paste.dxf]
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2015-09-03 RFM95/SPI code begun - won't compile yet.
    [rfm95w.c]
2015-09-09 Xtal osc, recalibrated delay_ms, added delay_us
    Most of #50, now need to make LCD use correct delays.
    [control.c, ignition.c, utils.c]
2015-09-09 Radio setup and SPI init code stuff, doesn't work
    [control.c, control_pins.h, control_radio.c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]
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2015-09-13 Made LCD delays more sensible. Resolves #50
    [display.c]
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2015-09-13 Output pin default values, resolves #54
    [control_pins.c, ignition_pins.c]
2015-09-14 Changed ADC to mv from V/10 to fix rounding bug
    [adc.c, adc.h, control.c]
2015-09-14 Wrote all of the packetisation stuff. CRC problems.
    [control.c, control_radio.c, ignition.c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]
2015-09-14 Fixed silly CRC err because tx packet len broke
    [control.c, ignition.c, rfm95w.c]
2015-09-15 Added async receive radio code, more crc problems
    [control.c, control_radio.c, ignition_radio.c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]
2015-09-16 Switched to boost PA to fix low tx power issue
    [rfm95w.c]
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2015-09-16 Fixed ADC issues, resolves #53
    Settling time was too low, reading to erroneous ADC readings.
    Clamp diode on continuity has 5uA leakage which, through the 10k limit
    resistor, gives a (somewhat variable) 50mV offset at low resistances, leading
    to 0ohms looking like 45-50ohms. Bodged this by subtracting the 50mV offset.
    [adc.c, ignition_radio.c]
2015-09-17 Wrote basic ignition buzzer DAC code (untested)
    Toward #55
    [ignition_pins.c, ignition_pins.h]
2015-09-18 Added control window CAM files
    [control_window_laser.dxf]
2015-09-18 Clock DAC periph, found good buzzer DAC values.
    [ignition_pins.c, ignition_pins.h]
2015-09-19 Fixed bug in control battery voltage rounding
    [control.c]
2015-09-19 Added systick timer/delays, resolves #56
    [control.c, ignition.c, utils.c]
2015-09-19 Added splash screens (normal/arm/wdt) resolves #64
    [control.c, control_pins.h]
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2015-09-22 RSSI value scaling. Resolves #60
    [control.c, control_radio.c, rfm95w.c]
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2015-09-22 Added actual key, fixed some consts
    [control_radio.c, ignition_radio.c]
2015-09-23 Ignition async mainloop, resolves #67
    [ignition.c, rfm95w.c]
2015-09-25 Packet loss/drop handling, resolves #69
    [control.c, control_radio.c, ignition.c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]
2015-09-25 Control display ignition channel firing status
    Resolves #68
    [control.c]
2015-09-25 Swapped both radios to 915MHz for USA usage
    [control.c, ignition.c]
2015-09-25 Buzzer volume settings
    Resolves #58
    [control.c, control_radio.c, ignition.c]
2015-09-29 Swapped both radios back to 868 for UK
    [control.c, ignition.c]
2017-01-29 Fixed whitespace style issues in C source/headers
    Mostly hard tabs instead of 4x spaces, and occasionally whitespace at
    the end of lines.
    [adc.c, adc.h, control.c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]
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2017-02-28 added various parts inc display
    [okgo3.kicad_pcb, okgo3.sch]
2017-03-01 Bump agg-kicad for nightly kicad fix
2017-08-18 Most of okgo2mini schematic
    [okgo2mini.kicad_pcb, okgo2mini.sch]
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2017-08-18 switches for okgo2 mini and usb
    [okgo2mini.sch, okgo2usbcontrol.sch]
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2017-08-18 Move slide swith to the correct board
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2017-08-19 footprints for okgo2mini and usbcontrol
    [okgo2mini.kicad_pcb, okgo2mini.sch, okgo2usbcontrol.kicad_pcb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]
2017-08-19 Minified parts, did some order codes
    [okgo2mini.sch, okgo2usbcontrol.sch]
2017-08-20 Very initial placement ideas
    [okgo2usbcontrol.kicad_pcb]
2017-08-20 Replace toggle switch on ignitionmini with slide
2017-08-20 Si5515 fire switch, DPDT switch 5V & batt
    [okgo2mini.sch]
